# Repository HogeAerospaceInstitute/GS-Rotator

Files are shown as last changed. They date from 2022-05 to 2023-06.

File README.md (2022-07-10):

# Ground Station Rotator Build
This page outlines the build process for a do-it-yourself rotator that comprises one of the hardware components of a groundstation for tracking objects in Low Earth Orbit. If you do not need to track orbital objects, you may consider going with a stationary design (e.g. geostationary weather satellites).

## Credit & Attribution
The rotator design is not a custom design, it follows the open-source plans provided by SATNOGS, specifically the SatNOGS Rotator v3 https://wiki.satnogs.org/SatNOGS_Rotator_v3. The main divergence, which will be discussed later, is the decision not to incorporate the SATNOGS circuit board and instead opting for a CNC board option, which drastically simplifies the electronics.

## Before Beginning
Right off the bat, this may seem like a large-scale project. In some ways, yes, it is...but that’s OK! I’ve done my best to try to break this project down into smaller pieces, i.e. rotator, antenna, final assembly, and getting telemetry data. The rotator alone cost ~300 USD. If in your situation, this feels like a little much for what you’re getting, consider constructing this with a group to split up costs. Trust me in that this is a perfect project for groups. This is not a 1-day project! Parts take time to procure, 3D printing takes time, and even the final assembly has a few pitfalls. You'll want to budget an ample amount of time and space to complete this project.

## Construction Order
Recommended Steps:
- Read through all the instructions
- Source the 3D parts first, these take the longest to fulfill & order. 
-- The Bill of Materials contains the quantity and parts you will need printed: https://gitlab.com/librespacefoundation/satnogs/satnogs-rotator/-/tree/master see `part-number-list.ods` and match it with the parts in `/rotator_parts`
- Purchase as many components as you can up front, you'll need them all eventually.
- Begin the Assemblies, and follow up with Control Hardware

## Reference Literature
Below is a list of URLs that were used in the construction of the antenna. This section will be updated as we progress through our project update installments. Spend some time browsing through these websites...you’ll be using them a lot as you build your groundstation. 
- Rotator design and instructions: https://wiki.satnogs.org/SatNOGS_Rotator_v3 
- Rotator repository (Contains the Bill of Materials or BOM as well as the CAD files necessary to 3D print components): https://gitlab.com/librespacefoundation/satnogs/satnogs-rotator 
- Controller board design and instructions: https://wiki.satnogs.org/SatNOGS_Arduino_Uno/CNC_Shield_Based_Rotator_Controller 
- Controller board repository (Files needed to flash the Arduino): https://gitlab.com/Quartapound/satnogs-rotator-firmware

## Design Choices
First, there are several options in the building of the rotator assembly. We recommend pursuing a build that incorporates stepper motors over dc motors as well as the CNC board over the SATNOGS custom circuit board for simplicity. The last decision is whether you wish to 3D print components yourself or send the CAD files to a company like Shapeways that will produce them for you. I utilized an Ender 3 3D printer. Another option is inquiring with a “Fab Lab” https://www.fablabs.io/labs/map, which typically have 3D printers, so all you would need to do is bring your CAD files with you and pay for cost of materials.

## Tools
I built my rotator assembly while keeping in mind to use as few exotic tools as possible. Inevitably, there are sometimes no substitutions for certain things, so I’ve listed what you’ll need below:
- Set of Metric hex wrenches
  - (If you end up purchasing a 3D printer, you might get these)
- Screwdriver set
- Voltmeter
  - (This is used to set the correct voltage on the stepper motor drivers)
- Wire Crimps
  - We’ll be splicing wires, so this allows us to connect wires to male pins on the CNC board. You specifically need ones that are for 2.54 pitch. We used these: https://www.amazon.com/gp/product/B06VWLW11G/ref=ppx_yo_dt_b_asin_titl e_o04_s00?ie=UTF8&psc=1
- A DC power supply
  - This allows you power the controller board with the necessary Voltage. We used this: https://www.amazon.com/gp/product/B08W293MJM/ref=ppx_yo_dt_b_asin_title_o03_s00?ie=UTF8&psc=1
- Soldering Iron
  - In addition to soldering wire connectors, this can be used to “heat press” nuts into some of the plastic 3D printed parts that came out slightly warped.
- Socket Wrench with metric 6 and 7
  - Makes life a bit easier with fastening bolts to nuts in some harder to reach areas (endstops)
- Wire strippers
  - You need ones that can strip 24-gauge wire that’s found in CAT 5 cable

## Assembly Info

### Shaft Side Assemblies - Qty 4
- Reference: https://wiki.satnogs.org/File:A1031-1.png, https://wiki.satnogs.org/File:A1032-1.png.
- Notes: You will need to construct 2 of A1031-1 and 2 of A1032-1. 
  - For A1032-1, simply omit the encoder mount as this is for the DC motor design. The pictures below are the fully constructed shaft side assemblies (A1031-1), which is a combination of two different 3D printed parts. The deep groove bearing can be press fit into the side shaft easily. The 3D printed recessions for the nuts can be difficult to press fit, and I found success using a soldering iron to heat up the nut which remelt the plastic recess in order to achieve a snug fit. If you find that a nut has too loose a fitting, utilizing Loctite can help secure the nut in place.

### Worm Gear Assembly - Qty 2
- Reference: https://wiki.satnogs.org/File:A1010-1.png
- Notes: Following the measurements is key here, otherwise this component may be misaligned with the worm wheel and cause degradation of components.

### Shaft Collar, Encoder Mount, Motor Mount, and Worm Gear Mount Assemblies
- Shaft Collar Reference: https://wiki.satnogs.org/File:A1020-1.png
- Encoder Mount Reference: https://wiki.satnogs.org/File:A1033-1.png
- Motor Mount Reference: https://wiki.satnogs.org/File:A1070-1.png
- Worm Gear Reference: https://wiki.satnogs.org/File:A1011.png
- Notes: I did not include individual photos of these assemblies, as the references are extremely straight forward with attaching bolts and press-fitting nuts and deep groove ball bearings into the various recesses in the 3D prints.

### Initial Frame and Attaching Worm Gear Mount
- Reference: https://wiki.satnogs.org/File:A1001-3.png

### Axis Pipe Assembly
- Reference: https://wiki.satnogs.org/File:A1030.png

### Lower Axis Pipe Assembly into Frame
- Reference: https://wiki.satnogs.org/File:A1040.png
- Notes: This is your opportunity to lubricate the worm wheel and worm gear components
with silicone grease to provide better rotation of the components.

### Joining the two frame assemblies together
- Reference: https://wiki.satnogs.org/File:A1050-1.png

# Control Hardware

### Wiring
With the assembled rotator, we next move to wiring. Here, we can cut off the ends of the CAT5 cable, cut the wire to desired length (I used roughly 2-3 feet), and strip 2 individual 24 guage wires that reside in the CAT5 cable. One end we leave the exposed stripped wire to be soldered on the endstops, and the other end we use a pair of crimps to attach female pin connectors and insert the pin connectors into 2 row connectors. Now we can solder the wires to the endstops. Below is an image of the type of mechanical endstop used:A few things to note here. You can see the body of the endstop 3 pins which are labeled “C” for common, “NO” for normally open, and “NC” for normally closed. When soldering we are looking to feed individual wires through the C and NO pins. Normally open means that we want to send a signal back to the controller board when the switch is depressed. Normally closed works opposite to that. These are probably the most finnicky components of the project. Initially, I had issues with the endstops not depressing enough to send a signal. My fix to this to glue a small a small shim of aluminum to the back to the endstop arm to along for better actuation.

### Power Supply
The controller board runs on 12-36V DC, so I elected to use a variable DC power supply and set voltage to 12V and amperage to 1A. There are a variety of ways to connect power to the controller board. I chose to take a pair of the bullclips that typically come with a variable power supply, cut off the clip, and use twist style wire connectors to join additional cable. This additional cable was then stripped and can simply be inserted directly into the screwdriver cable clamps on the controller board.

### Flashing the Arduino
We now need to load the libraries and code necessary to allow the rotator to respond to commands. This is the point where we need to download the SATNOGs firmware. Download as a zip file and unzip it. Here, we open the Arduino IDE and we are opening up a file called “stepper_motor_controller.ino” in the stepper motor controller folder. Once open, connect your Arduino board to your computer with the USB cable. You can notice that on the bottom right corner of the IDE window a statement that reads “Arduino Uno on COMX”, where X is some number. In my case it was 3, but this may differ for you. We now need to include an additional library called AccelStepper. Under Sketch, select “Include Library”, and select “Manage Libaries”. Type in AccelStepper in the search bar and select install. Now, with the .ino file open, hit the checkmark icon on the top of the tool bar to verify. After verifying, hit the right arrow button to upload the firmware to the Arduino. After successfully uploading, we can now disconnect the Arduino from the computer. Assembling rotator controller From here, we can attach the stepper motor drivers to the CNC board, and from here, attach the CNC board on top of the Arduino. Reference: https://wiki.satnogs.org/images/a/a4/Assembled_CNC_Shield.png

### Crazy CNC board pin configurations and wiring everything else up
If you purchase the exact same CNC board as I included in a URL, the pin configuration numbers do not match the .ino file we just uploaded to the Arduino. In order to complete this project with minimal programming and we can naively connect the wires to the header pins. To do this, connect the azimuth (vertical pipe) stepper motor wiring to the X stepper motor driver and its associated endstop wiring to either Z+ or Z-. Next connect the elevation (horizontal pipe)stepper motor wiring to the Y stepper motor driver and its associated endstop wiring to either X+ or X-. Yes, I know it’s silly, but it’s probably an easier solution that drilling down in a header file and making the correction...

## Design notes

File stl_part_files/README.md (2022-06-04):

# Custom Parts for Ground Station Rotator
This folder contains the STL mesh files for fabrication of parts necessary to build an azimuth/elevation rotator for tracking objects in low earth orbit. The designs are taken and potentially modified from the SatNOGS Rotator v3 release https://gitlab.com/librespacefoundation/satnogs/satnogs-rotator/ and follow the licensing guidelines set there-in.

## 3D Printing Notes
This guide is written for 3D printing of the included parts with a **PLA** filament extrusion machine. It has been successfully completed with a base model Ender 3 and a 0.4mm nozzle with appropriate layer heights. Later that nozzle was upgraded to 0.6mm and the layer heights adjusted. The parts to be printed comprise a working gearbox and mounts for transferring power from a stepper motor to an aluminum tube. 

### Tolerances
Many of the parts are designed to press fit bearings or hexagonal nuts. The hexagonal nuts can be set with acrylic glue (super glue) if the recess is too large, or eased in with heating from a soldering iron if the recess is too small. The press-fit bearings are generally forgiving if the tolerance is within -0.20mm, +0.05mm. Recesess too large on the bearing fits is not ideal, and should be avoided. A cheap set of calipers can help you troubleshoot any problems.

The biggest determining tolerance is the 40mm diameter set by the aluminum tube. The parts **C1020-1, C1021-1, C1022-3, C1040-2** all fit directly onto the tube, and thus must slightly be larger than 40mm. Because these parts are locked in place by set screws, it was found that 40.5mm was an acceptable inner diameter for the parts, yielding a tolerance of +0.5mm.

General rule of thumb:
- Exact size or +1% scale on bearing parts
- +1.5% scaling on aluminum tube mounted parts

### Materials
ABS and PETG are generally considered to be more durable than PLA but have different shrinkage rates upon cooling. The notes below are set for PLA, you may need to adjust as necessary.

### Layer Heights & Overhangs
0.4mm or smaller is recommended for layer heights, and any gear mating surfaces should be free of defects and blemishes. After construction and operation, the mating surfaces will wear down, deburring each other. However the surfaces should not abrade completely if the machine is to continue operating reliably.

The helical gear **C1062-1** is by far the hardest piece to print, and contains either overhangs or support structures. I was able to print it without supports after adjusting the layer height (0.15mm on 0.4mm nozzle), retraction, cooling fan, and temperature to prevent the edges from curling. If you have severe difficulty with this part, consider printing on its side with support and using a file to smooth.

### Changes from SatNOGS Specs
**C1040-2, C1042-2** have been modified from the original SatNOGS specification. **C1040-2** contains a tongue that triggers an infrared optical switch for the end stop. This tongue will likely need some sanding for smooth operation. **C1042-2** is the mount for the optical switch.

## Bill of Materials - What to Print
The same information is contained in *Parts List.ods*.

You can use https://wiki.satnogs.org/SatNOGS_Rotator_v3 as a reference for what the parts will look like, although two of the parts (**C1040, C1042**) have changed.

| Part Number | Description | Quantity | Comments |
|---| :--- | :---: |---|
| `C1010-3_bearing_mount` | Deep groove ball bearing 6008zz mount | 4 | 101% scaling, 0.4mm layer height |
| `C1011-3_bearing_cover` | End cap bearing cover for `C1010-3` | 4 | 101% scaling, match `C1010-3` |
| `C1020-1_shaft_gear` | Worm wheel axis gear 30T | 2 | 101.5% scaling, 0.4mm layer height |
| `C1021-1_shaft_collar` | Locking collar for `C1020-1` | 2 | 101.5% scaling, 0.4mm layer height, match `C1020` |
| `C1022-3_shaft_spacer` | Shaft spacer for `C1020-1` | 2 | 101.5% scaling, match `C1020` |
| `C1030-1_motor_mount` | Stepper motor mount | 2 | 101% scaling, must press fit motor but match screw holes on NEMA17 motor. Print with support |
| `C1040-2_locking_collar` | Collar & Endstop tongue | 2 | 101.5% scaling, print with support for tongue but will need filing |
| `C1042-2_endstop_mount` | Mount for optical endstop sensor | 2 | Match `C1010-3` properties |
| `C1061-5_worm_mount` | Bearing press fit for mounting worm gear | 2 | Layer height 0.4mm, 100% scale was fine |
| `C1061-6_worm_mount_mirror` | Mirror part to `C1061-5` | 2 | Match `C1061-5` |
| `C1062-1_worm_gear` | Worm gear | 2 | Print as cleanly as possible, no defects, 100% scale |
| `C1083-1_shaft_seal` | Shaft seal | 3 | Layer height 0.4mm, 101.5% scale |
| `C1084-1_screw_spacer` | Spacer for screws on case | 4 | Layer height 0.4mm |

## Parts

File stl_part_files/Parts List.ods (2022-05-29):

Part Number | Description | Comments | QTY
C1010-3_bearing_mount | Shaft deep groove ball bearing 6008zz mount | Layer height 0.4mm | 4
C1011-3_bearing_cover | Shaft deep groove ball bearing 6008zz mount | Layer height 0.4mm | 4
C1020-1_shaft_gear | Worm wheel gear, 30T | Layer height 0.4mm | 2
C1021-1_shaft_collar | Worm wheel mount | Layer height 0.4mm, metric/imperial option | 2
C1022-3_shaft_space | Spacer or washer for shaft | Layer height 0.4mm or laser cuted | 2
C1030-1_motor_mount | Motor mount | Layer height 0.4mm | 2
C1040-2_locking_collar | Contains tongue for optical sensor | Layer height 0.4mm, metric/imperial option | 2
C1042-2_endstop_mount | End stop mount | Layer height 0.4mm | 2
C1061-5_worm_mount | Worm mount | Layer height 0.4mm | 2
C1061-6_worm_mount_mirror | worm mount mirror part | Layer height 0.4mm | 2
C1062-1_worm_gear | Worm gear, is laser sintering part with nylon plastic | Laser sintering part, shapeways | 2
C1083-1_shaft_seal | Shaft seal | Layer height 0.4mm, metric/imperial option | 3
C1084-1_screw_spacer | Spacer for C1080 to use M4 L10 screws | Layer height 0.4mm | 4

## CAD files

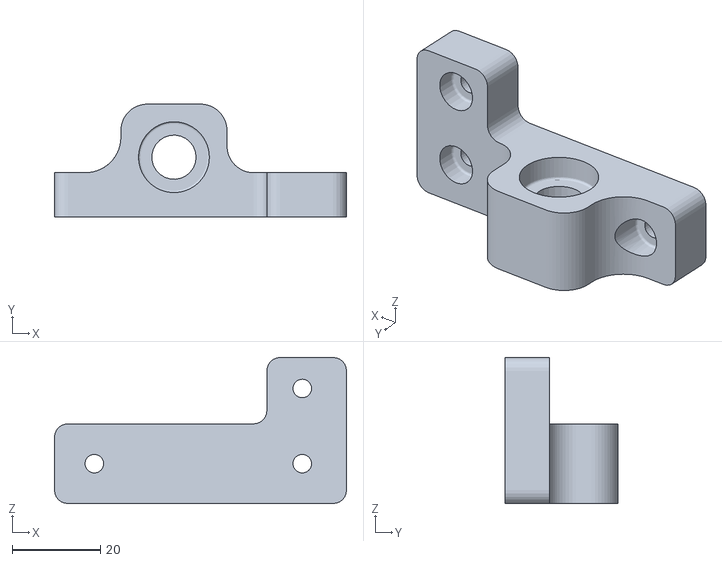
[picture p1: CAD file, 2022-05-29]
stl_part_files/C1061-6_worm_mount_mirror.stl
66.0 x 25.5 x 33.0

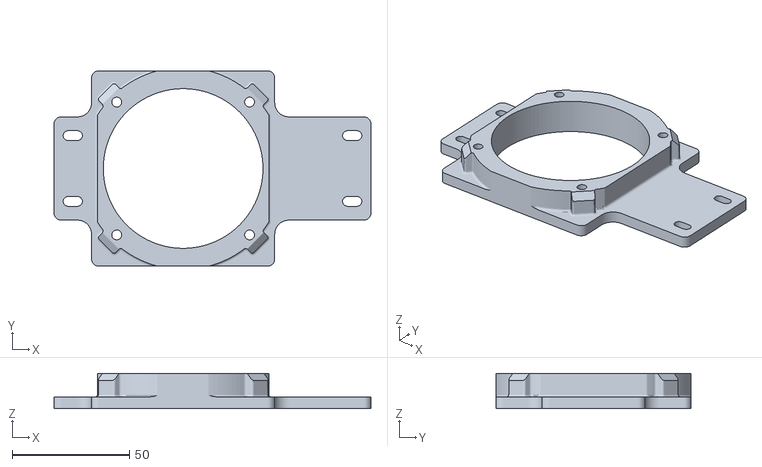
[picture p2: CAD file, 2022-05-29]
stl_part_files/C1010-3_bearing_mount.stl
135.0 x 83.2 x 15.0

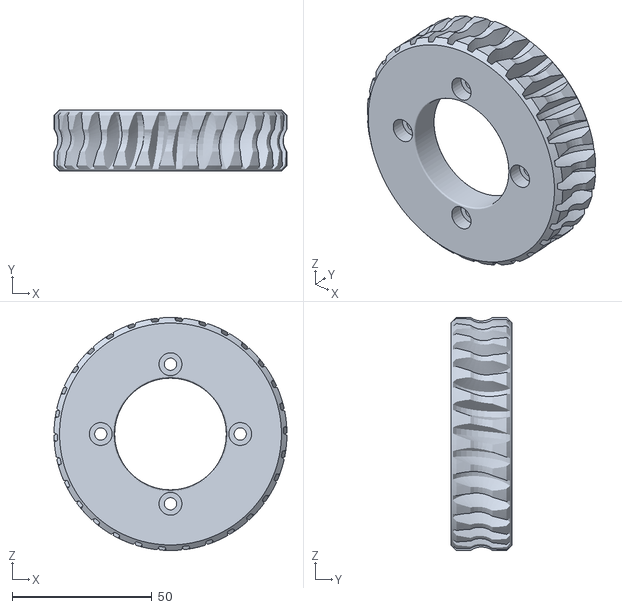
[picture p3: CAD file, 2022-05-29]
stl_part_files/C1020-1_shaft_gear.stl
83.5 x 22.0 x 83.5

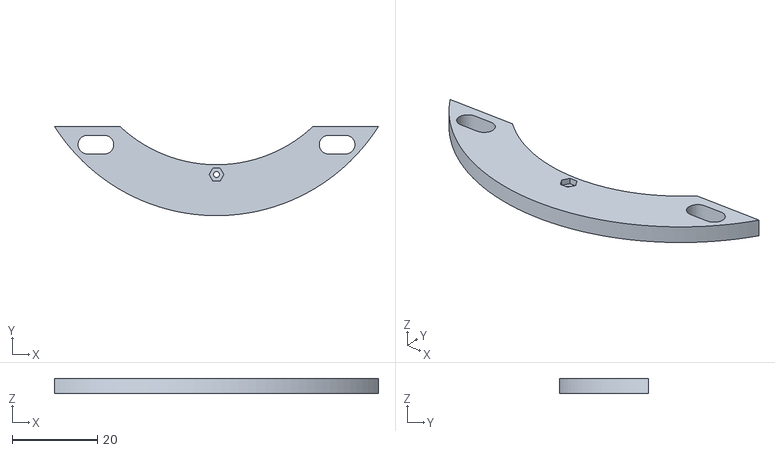
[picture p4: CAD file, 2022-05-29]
stl_part_files/C1042-2_endstop_v2.stl
76.0 x 20.9 x 3.50

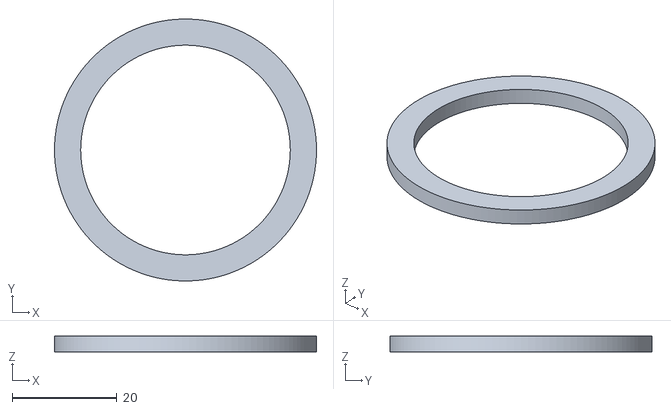
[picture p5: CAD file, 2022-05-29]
stl_part_files/C1022-3_shaft_spacer.stl
50.0 x 50.0 x 3.00

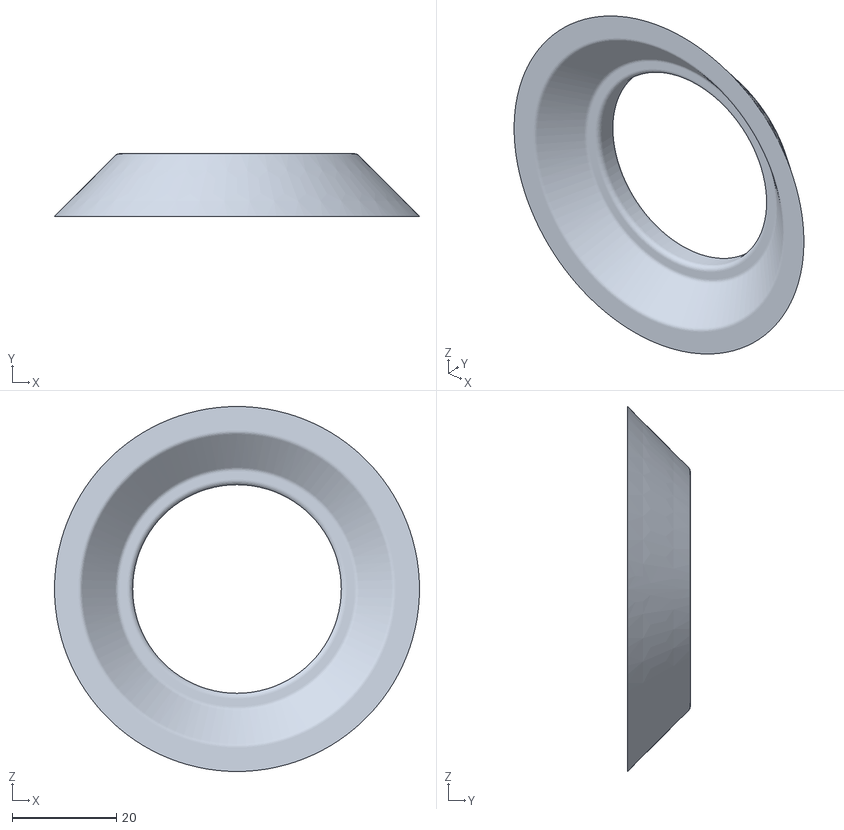
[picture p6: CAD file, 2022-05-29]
stl_part_files/C1083-1_shaft_seal.stl
70.0 x 12.0 x 70.0

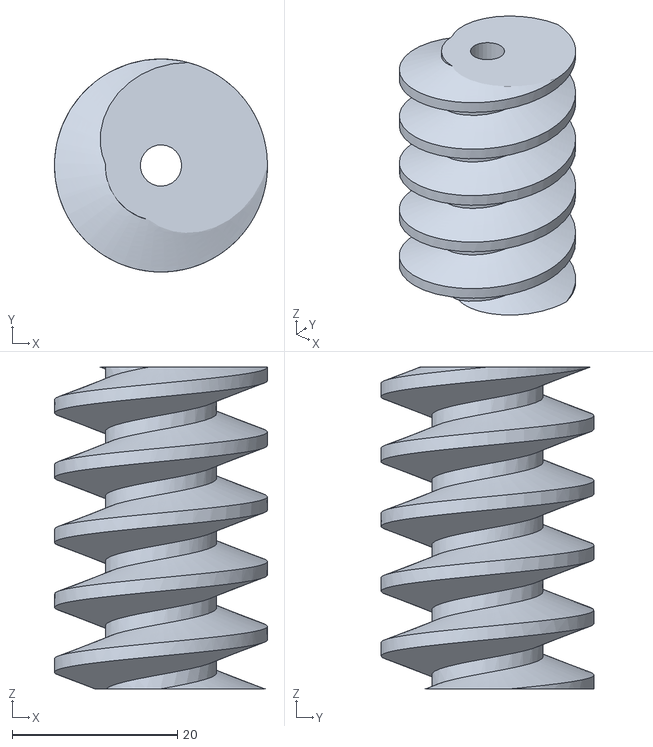
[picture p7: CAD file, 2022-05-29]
stl_part_files/C1062-1_worm_gear.stl
25.8 x 25.8 x 39.0

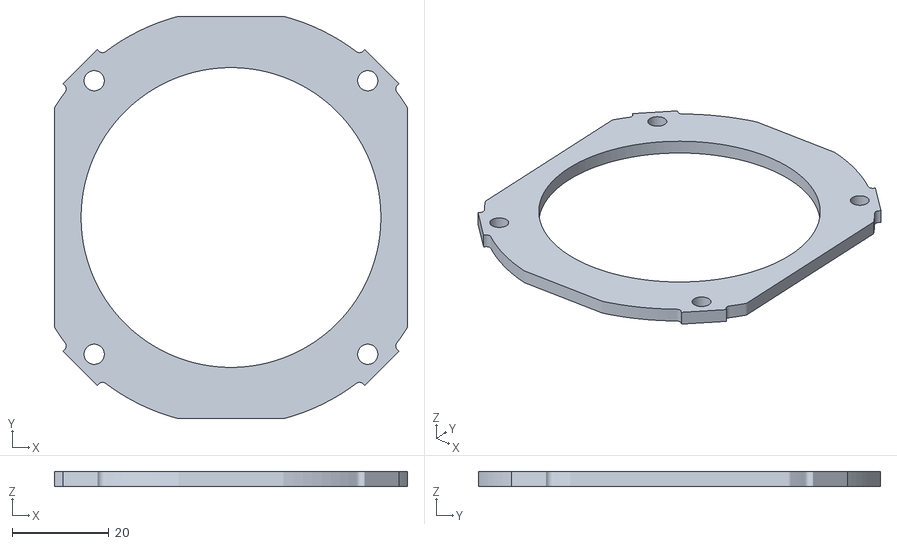
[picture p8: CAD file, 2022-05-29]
stl_part_files/C1011-3_bearing_cover.stl
73.0 x 83.2 x 3.00

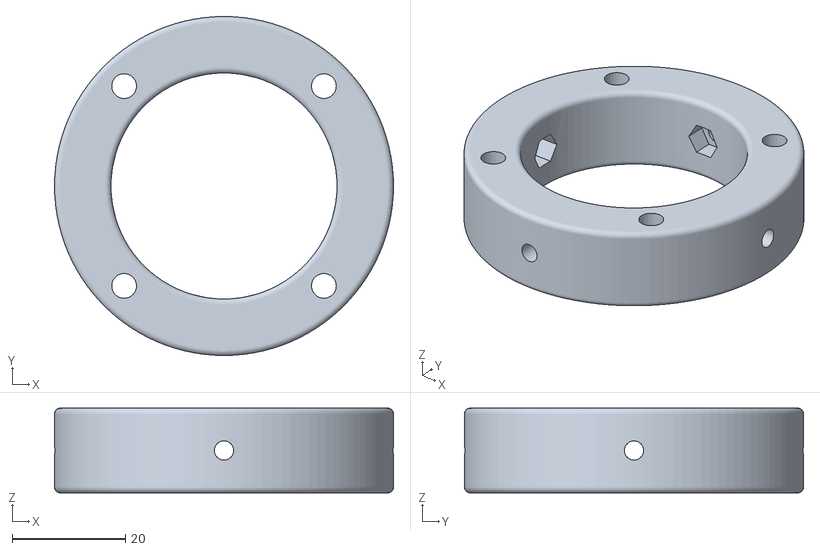
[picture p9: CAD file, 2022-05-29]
stl_part_files/C1021-1_shaft_collar.stl
60.0 x 60.0 x 15.0

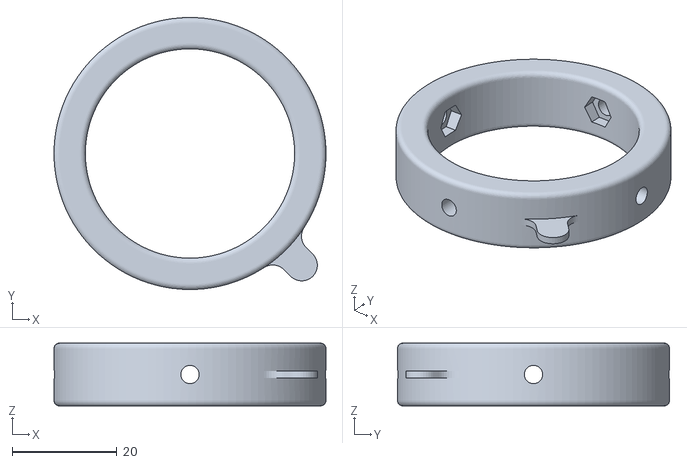
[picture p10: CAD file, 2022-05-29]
stl_part_files/C1040-2_locking_collar.stl
52.0 x 52.0 x 12.0

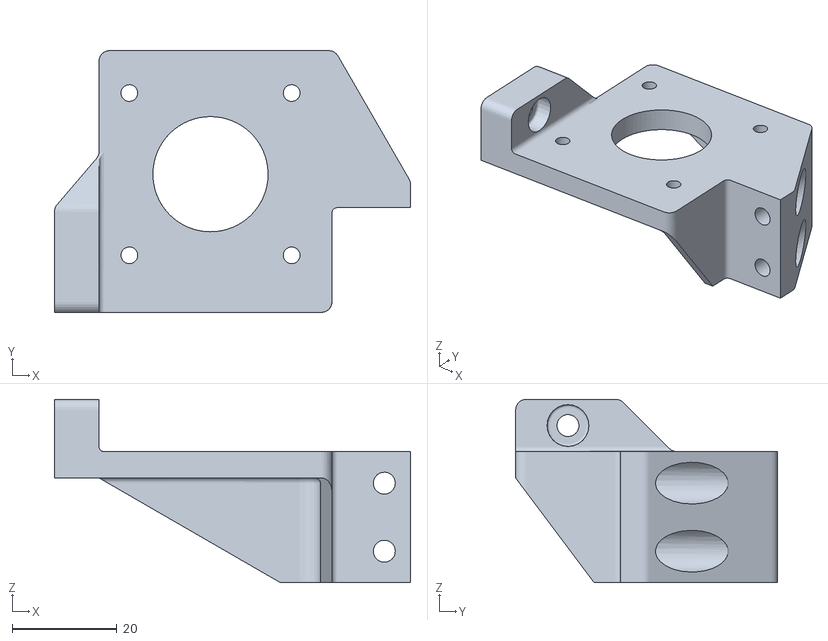
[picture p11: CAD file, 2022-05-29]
stl_part_files/C1030-1_motor_mount.stl
68.0 x 50.0 x 35.0

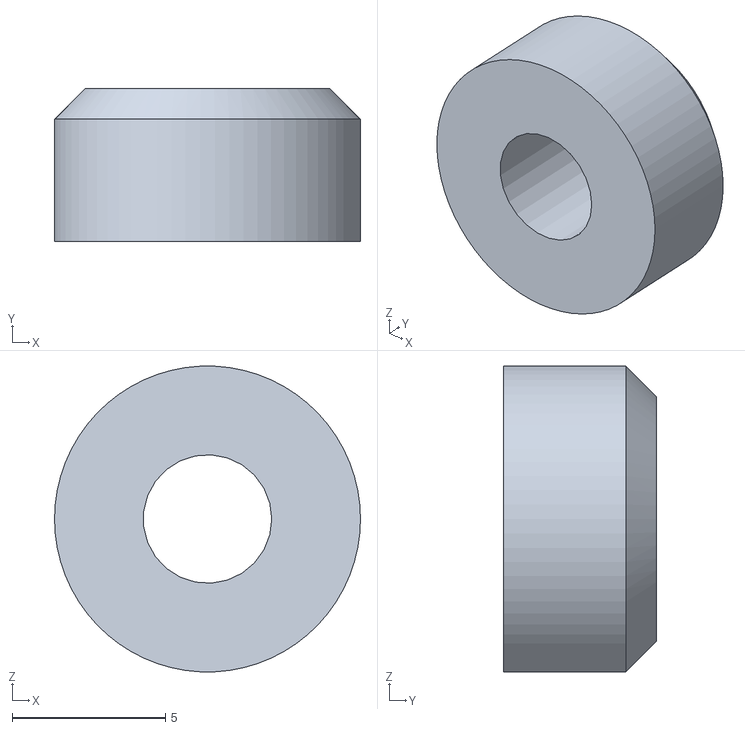
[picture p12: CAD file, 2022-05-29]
stl_part_files/C1084-1_screw_spacer.stl
10.0 x 5.00 x 9.99

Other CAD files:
stl_part_files/C1061-5_worm_mount.stl

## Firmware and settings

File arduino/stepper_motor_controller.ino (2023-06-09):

/*!
 * @file stepper_motor_controller.ino
 *
 * This is the documentation for satnogs rotator controller firmware
 * for stepper motors configuration. The board (PCB) is placed in
 * <a href="https://gitlab.com/librespacefoundation/satnogs/satnogs-rotator-controller">
 * satnogs-rotator-controller </a> and is for releases:
 * v2.0
 * v2.1
 * v2.2
 * <a href="https://wiki.satnogs.org/SatNOGS_Rotator_Controller"> wiki page </a>
 *
 * @section dependencies Dependencies
 *
 * This firmware depends on <a href="http://www.airspayce.com/mikem/arduino/AccelStepper/index.htmlhttp://www.airspayce.com/mikem/arduino/AccelStepper/index.html">
 * AccelStepper library</a> being present on your system. Please make sure you
 * have installed the latest version before using this firmware.
 *
 * @section license License
 *
 * Licensed under the GPLv3.
 *
 */

#define SAMPLE_TIME        0.1   ///< Control loop in s
#define RATIO              108    ///< Gear ratio of rotator gear box                                 default 54
#define MICROSTEP          8     ///< Set Microstep
#define MIN_PULSE_WIDTH    20    ///< In microsecond for AccelStepper
#define MAX_SPEED          3200  ///< In steps/s, consider the microstep
#define MAX_ACCELERATION   1600  ///< In steps/s^2, consider the microstep
#define SPR                1600L ///< Step Per Revolution, consider the microstep
#define MIN_M1_ANGLE       0     ///< Minimum angle of azimuth
#define MAX_M1_ANGLE       360   ///< Maximum angle of azimuth
#define MIN_M2_ANGLE       0     ///< Minimum angle of elevation
#define MAX_M2_ANGLE       180   ///< Maximum angle of elevation
#define DEFAULT_HOME_STATE HIGH  ///< Change to LOW according to Home sensor
#define HOME_DELAY         12000 ///< Time for homing Deceleration in millisecond

#include <AccelStepper.h>
#include <Wire.h>
#include "globals.h"
#include "easycomm.h"
#include "rotator_pins.h"
//#include <rs485.h>
#include "endstop.h"
//#include <watchdog.h>

uint32_t t_run = 0; // run time of uC
easycomm comm;
AccelStepper stepper_az(1, M1IN1, M1IN2);
AccelStepper stepper_el(1, M2IN1, M2IN2);
endstop switch_az(SW1, DEFAULT_HOME_STATE), switch_el(SW2, DEFAULT_HOME_STATE);
//wdt_timer wdt;

enum _rotator_error homing(int32_t seek_az, int32_t seek_el);
int32_t deg2step(float deg);
float step2deg(int32_t step);

void setup() {
    // Homing switch
    switch_az.init();
    switch_el.init();

    // Serial Communication
    comm.easycomm_init();

    // Stepper Motor setup
    stepper_az.setEnablePin(MOTOR_EN);
    stepper_az.setPinsInverted(false, false, true);
    stepper_az.enableOutputs();
    stepper_az.setMaxSpeed(MAX_SPEED);
    stepper_az.setAcceleration(MAX_ACCELERATION);
    stepper_az.setMinPulseWidth(MIN_PULSE_WIDTH);
    stepper_el.setPinsInverted(false, false, true);
    stepper_el.enableOutputs();
    stepper_el.setMaxSpeed(MAX_SPEED);
    stepper_el.setAcceleration(MAX_ACCELERATION);
    stepper_el.setMinPulseWidth(MIN_PULSE_WIDTH);

    // Initialize WDT
    // wdt.watchdog_init();
}

void loop() {
    // Update WDT
   // wdt.watchdog_reset();

    // Get end stop status
    rotator.switch_az = switch_az.get_state();
    rotator.switch_el = switch_el.get_state();

    // Run easycomm implementation
    comm.easycomm_proc();

    // Get position of both axis
    control_az.input = step2deg(stepper_az.currentPosition());
    control_el.input = step2deg(stepper_el.currentPosition());

    // Check rotator status
    if (rotator.rotator_status != error) {
        if (rotator.homing_flag == false) {
            // Check home flag
            rotator.control_mode = position;
            // Homing
            rotator.rotator_error = homing(deg2step(-MAX_M1_ANGLE),
                                           deg2step(-MAX_M2_ANGLE));
            if (rotator.rotator_error == no_error) {
                // No error
                rotator.rotator_status = idle;
                rotator.homing_flag = true;
            } else {
                // Error
                rotator.rotator_status = error;
                rotator.rotator_error = homing_error;
            }
        } else {
            // Control Loop
            stepper_az.moveTo(deg2step(control_az.setpoint));
            stepper_el.moveTo(deg2step(control_el.setpoint));
            rotator.rotator_status = pointing;
            // Move azimuth and elevation motors
            stepper_az.run();
            stepper_el.run();
            // Idle rotator
            if (stepper_az.distanceToGo() == 0 && stepper_el.distanceToGo() == 0) {
                rotator.rotator_status = idle;
            }
        }
    } else {
        // Error handler, stop motors and disable the motor driver
        stepper_az.stop();
        stepper_az.disableOutputs();
        stepper_el.stop();
        stepper_el.disableOutputs();
        if (rotator.rotator_error != homing_error) {
            // Reset error according to error value
            rotator.rotator_error = no_error;
            rotator.rotator_status = idle;
        }
    }
}

/**************************************************************************/
/*!
    @brief    Move both axis with one direction in order to find home position,
              end-stop switches
    @param    seek_az
              Steps to find home position for azimuth axis
    @param    seek_el
              Steps to find home position for elevation axis
    @return   _rotator_error
*/
/**************************************************************************/
enum _rotator_error homing(int32_t seek_az, int32_t seek_el) {
    bool isHome_az = false;
    bool isHome_el = false;

    // Move motors to "seek" position
    stepper_az.moveTo(seek_az);
    stepper_el.moveTo(seek_el);

    // Homing loop
    Serial.println("Homing...");
    while (isHome_az == false || isHome_el == false) {
        // Update WDT
       // wdt.watchdog_reset();=
        if (switch_az.get_state() == true && !isHome_az) {
            Serial.println("Az is home");
            // Find azimuth home
            stepper_az.moveTo(stepper_az.currentPosition());
            isHome_az = true;
        }
        if (switch_el.get_state() == true && !isHome_el) {
            Serial.println("El is home");
            // Find elevation home
            stepper_el.moveTo(stepper_el.currentPosition());
            isHome_el = true;
        }
        // Check if the rotator goes out of limits or something goes wrong (in
        // mechanical)
        if ((stepper_az.distanceToGo() == 0 && !isHome_az) ||
            (stepper_el.distanceToGo() == 0 && !isHome_el)){
            return homing_error;
        }
        Serial.println(switch_az.get_state());
        
        // Move motors to "seek" position
        stepper_az.run();
        stepper_el.run();
    }
    // Delay to Deccelerate and homing, to complete the movements
    uint32_t time = millis();
    while (millis() - time < HOME_DELAY) {
       // wdt.watchdog_reset();
        stepper_az.run();
        stepper_el.run();
    }
    // Set the home position and reset all critical control variables
    stepper_az.setCurrentPosition(0);
    stepper_el.setCurrentPosition(0);
    control_az.setpoint = 0;
    control_el.setpoint = 0;

    return no_error;
}

/**************************************************************************/
/*!
    @brief    Convert degrees to steps according to step/revolution, rotator
              gear box ratio and microstep
    @param    deg
              Degrees in float format
    @return   Steps for stepper motor driver, int32_t
*/
/**************************************************************************/
int32_t deg2step(float deg) {
    return (RATIO * SPR * deg / 360);
}

/**************************************************************************/
/*!
    @brief    Convert steps to degrees according to step/revolution, rotator
              gear box ratio and microstep
    @param    step
              Steps in int32_t format
    @return   Degrees in float format
*/
/**************************************************************************/
float step2deg(int32_t step) {
    return (360.00 * step / (SPR * RATIO));
}
